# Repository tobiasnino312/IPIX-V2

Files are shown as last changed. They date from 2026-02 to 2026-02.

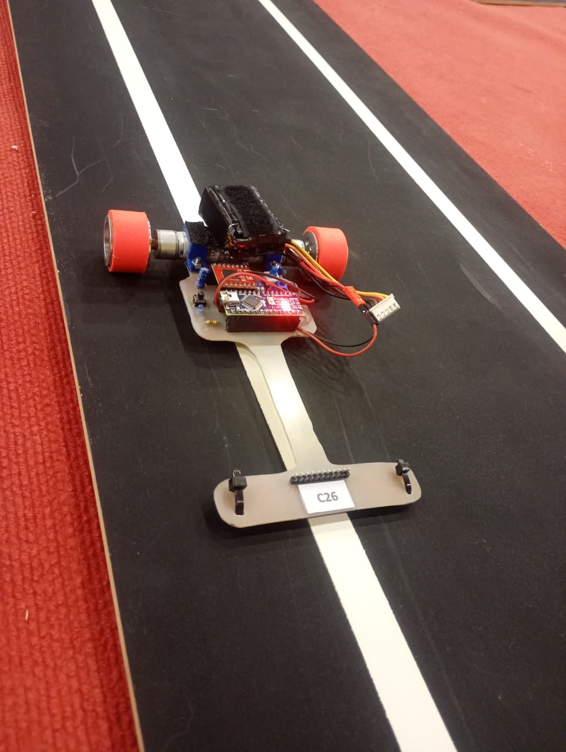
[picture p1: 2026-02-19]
IPIX_V2.jpeg

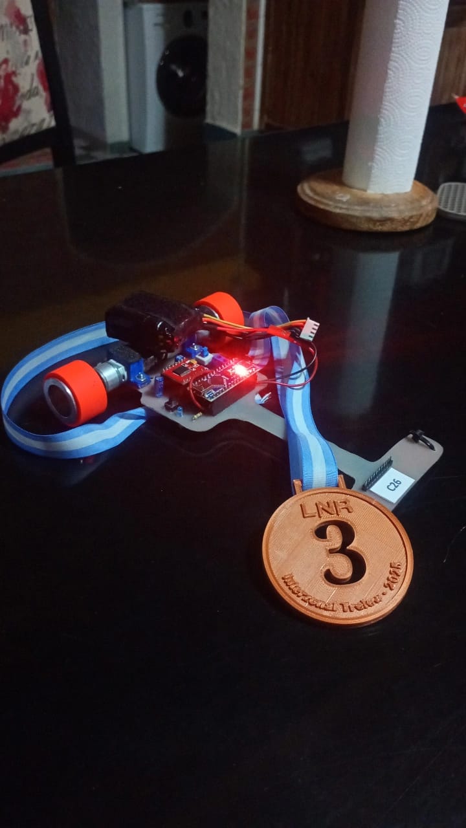
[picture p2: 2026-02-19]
IPIX_3ERO.jpeg

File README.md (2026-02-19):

# IPIX-V2
Robot seguidor de línea utilizado desde el 30/08/2025 en el interzonal de Trelew de la LNR argentina con un 3° puesto interzonal. 
El mismo trabaja con el microcontrolador Arduino Nano, TB6612FNG, motores ProFast de 4000rpm, una bateria LiPo 4s 600mAh armada casera, llantas y cubiertas JSUMO SLT20 y una regleta de sensores QTR8A genérica, similar a la de Pololu. 
Posee un switch DIP para selección de estrategias o configuraciones (empleado para cambio de velocidad según interior o exterior de la pista) y una programación basada en PID básico. 
En cuanto al código, se probó un sistema con intervalos de tiempo para el control dinámico de velocidades base/máximas o parámetros de cálculo del PID, pero debido al poco tiempo de pruebas en pista no se pudo aprovechar. Además, se está desarrollando un algoritmo con Twiddle (un algoritmo de tuning de PID con una especie de aprendizaje escalonado muy básico) que aún no fue probado en pista, con el objetivo de optimizar el tiempo de pruebas en competencia y recopilar datos de tiempo de vuelta y constantes del cálculo del PID.
Por otro lado, se está avanzando con el diseño de una tercera versión (IPIX V3) migrando a una BluePill (STM32F103C8T6), RZ7899 como drivers de motores, hueco para una turbina para mayor adherencia (la limitante actual del prototipo) y 10 sensores QRE1113 directamente soldados a placa con lectura directa por cada canal del ADC disponible.

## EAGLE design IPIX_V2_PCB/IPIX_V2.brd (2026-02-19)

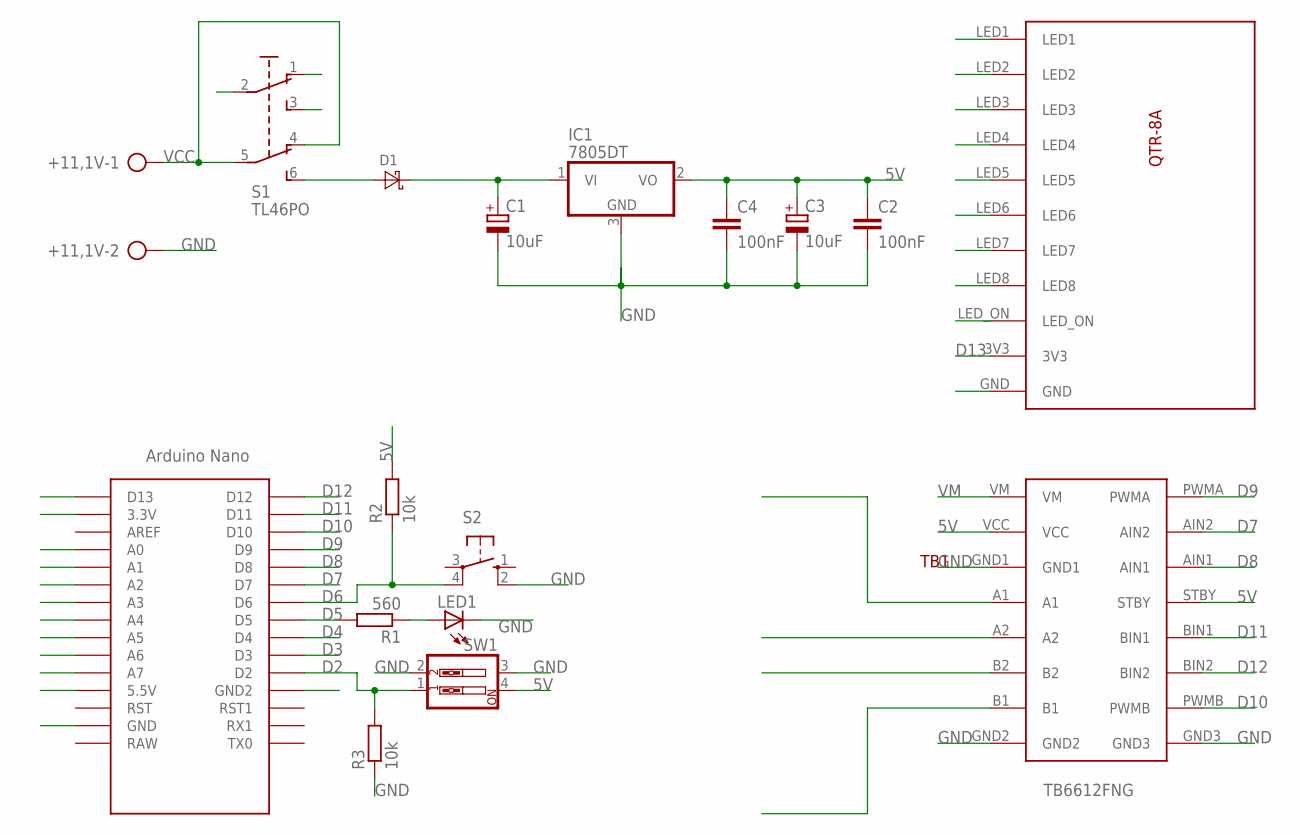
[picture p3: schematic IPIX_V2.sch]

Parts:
+11,1V: AK500/2-H
C1, C3: 10uF; E2,5-6E
C2, C4: 100nF; C0805
D1: DIODE-SCHOTTKY-DO201AD; DO201AD
IC1: 7805DT; TO252
LED1: LED3MM
R1: 560; 0204/7
R2, R3: 10k; R0805
S1: TL46PO; TL4XPO
S2: 10-XX; B3F-10XX
SW1: SW_DIP-2; EDG-02
TB1: TB6612FNG
U$1: NANO
U$2: QTR-8A

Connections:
3,3V: U$1.3.3V
5V: C2.1, C3.+, C4.1, IC1.2 (VO), R2.2, SW1.4, TB1.STBY, TB1.VCC, U$1.5V (5.5V), U$2.LED8
A0: U$1.A0, U$2.LED_ON
A1: U$1.A1, U$2.LED1
A2: U$1.A2, U$2.LED2
A3: U$1.A3, U$2.LED3
A4: U$1.A4, U$2.LED4
A5: U$1.A5, U$2.LED5
A6: U$1.A6, U$2.LED6
A7: U$1.A7, U$2.LED7
D2: R3.2, SW1.1, U$1.D2
D3: U$1.D3
D4: U$1.D4
D5: R1.2, U$1.D5
D6: R2.1, S2.4 (P1), U$1.D6
D7: TB1.AIN2, U$1.D7
D8: TB1.AIN1, U$1.D8
D9: TB1.PWMA, U$1.D9
D10: TB1.PWMB, U$1.D10
D11: TB1.BIN1, U$1.D11
D12: TB1.BIN2, U$1.D12
D13: U$1.D13, U$2.3V3
GND: +11,1V.2, C1.-, C2.2, C3.-, C4.2, IC1.3 (GND), LED1.K (C), R3.1, S1.1 (O), S1.2, S1.3 (S), S2.2 (S1), SW1.2, SW1.3, TB1.GND1, TB1.GND2, TB1.GND3, U$1.GND, U$1.GND1 (GND2), U$2.GND
unnamed: D1.A, S1.6 (S1)
unnamed 24: TB1.A2; also elsewhere on the board
unnamed 25: TB1.A1; also elsewhere on the board
unnamed: LED1.A, R1.1
unnamed 42: TB1.B2; also elsewhere on the board
unnamed 43: TB1.B1; also elsewhere on the board
VCC: +11,1V.1, S1.4 (O1), S1.5 (P1)
VM: C1.+, D1.C, IC1.1 (VI), TB1.VM

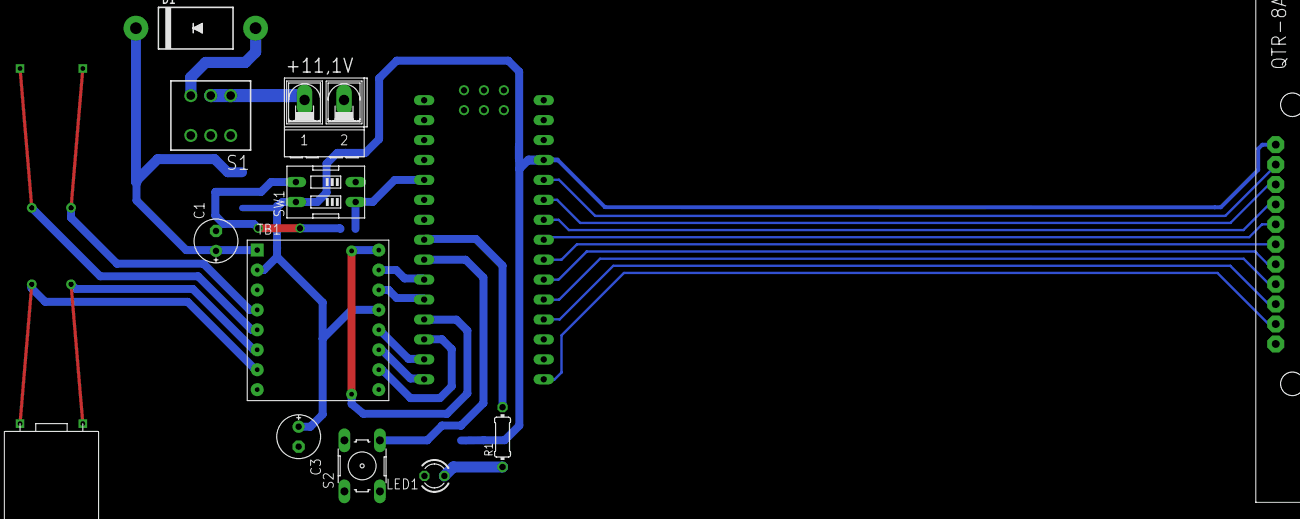
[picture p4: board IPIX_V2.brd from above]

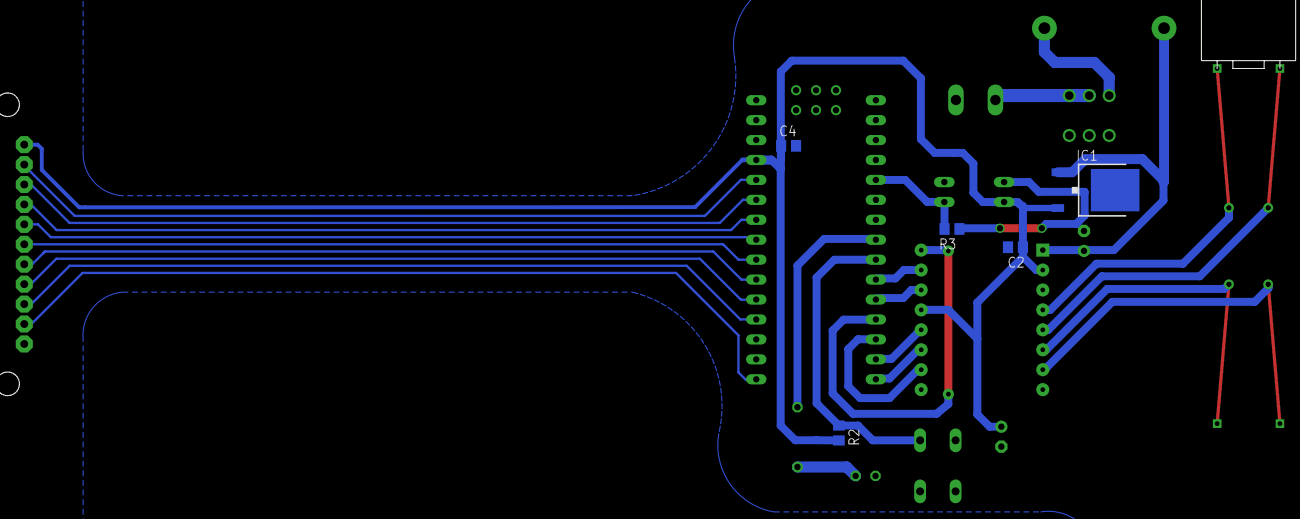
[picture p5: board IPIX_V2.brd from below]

Board: 2 copper layers, 19 parts (6 on the bottom side), 28 nets.

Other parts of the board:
U$3, U$4: MOTOR_N20

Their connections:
unnamed 24: U$3.M2; also elsewhere on the board
unnamed 25: U$3.M1; also elsewhere on the board
unnamed 42: U$4.M1; also elsewhere on the board
unnamed 43: U$4.M2; also elsewhere on the board

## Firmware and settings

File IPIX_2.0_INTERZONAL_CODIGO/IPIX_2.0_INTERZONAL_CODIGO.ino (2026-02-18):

//CODIGO UTILIZADO CON EL ROBOT IPITS 2.0 EN COMPETENCIA INTERZONAL DE ROBOTICA EL 31/08/2025 CON UN RESULTADO FINAL DE UN 3°ER PUESTO//
//LIBRERIAS//
#include <QTRSensors.h>

//SENSORES QTR8A//
QTRSensors qtr;
const uint8_t SensorCount = 8;
uint16_t sensorValues[SensorCount];

//DEFINICIONES DE PINES//
#define PWMder 10
#define IN1der 11 
#define IN2der 12
#define PWMizq 9
#define IN1izq 8
#define IN2izq 7
#define DIP 2
#define LED 5
#define BTN 6
#define IR 13

int estado=0;
int VDER, VIZQ, linea, errorant, error, integral, derivativa, velocidad, VMAX;
float kp, ki, kd, correccion;

//INTERVALOS DE TIEMPOS SENGUN SECTOR DE LA PISTA//
int tiempoinicio=0;
int tiempoactual=0;
int tiempo1=3000;
int tiempo2=999999;
int tiempo3=999999;
int tiempo4=999999;
int tiempo5=999999;
int tiempo6=999999;
int VMIN = 80;
int VEL = 80;

void setup() {
  // Fast PWM con TOP = ICR1
  TCCR1A = _BV(COM1A1) | _BV(COM1B1) | _BV(WGM11);
  TCCR1B = _BV(WGM13) | _BV(WGM12) | _BV(CS10); // prescaler = 1
  ICR1 = 999; // → 16 kHz exacto

  OCR1A = 0; // Motor A (pin 9)
  OCR1B = 0; // Motor B (pin 10)

//SENSORES//
qtr.setTypeAnalog();
qtr.setSensorPins((const uint8_t[]){A0, A1, A2, A3, A4, A5, A6, A7}, SensorCount);

//PINOUTS// 
pinMode(PWMder,OUTPUT);
pinMode(PWMizq,OUTPUT);
pinMode(IN1der,OUTPUT);
pinMode(IN2der,OUTPUT);
pinMode(IN1izq,OUTPUT);
pinMode(IN2izq,OUTPUT);
pinMode(LED,OUTPUT);
pinMode(BTN,INPUT);
pinMode(DIP,INPUT);
pinMode(IR,OUTPUT);

//ACTIVACION DE LEDS DE SENSORES//
digitalWrite(IR,1);
//LECTURA DIP//
if (digitalRead(DIP)==1){
    kp=0.35;
    ki=0.05;
    kd=38;    
    velocidad=80;
    VMAX=160; 
  }
  else{      
//I (Interior)
    kp=0.35;
    ki=0.05;
    kd=38;    
    velocidad=70;
    VMAX=140; 
  }
//ARRANQUE CALIBRACION//
while (true){
  if ((digitalRead(BTN)==0) && estado==0){
    delay(100);
    calibracion(); 
    estado=1;
    }
  if ((digitalRead(BTN)==0) && estado==1){
    digitalWrite(LED,1);
    tiempoinicio=millis();
    break;
    }
  }
}

void loop() {
  sensores();
  PID();
  MOTORES();
}

void tiempo(){
  tiempoactual = millis() - tiempoinicio;
  if(tiempoactual>=tiempo1){
    if(tiempoactual>=tiempo2){
      if(tiempoactual>=tiempo3){
        if(tiempoactual>=tiempo4){
          if(tiempoactual>=tiempo5){
           if(tiempoactual>=tiempo6){
            VMAX=170;
            velocidad=VMIN;
            }  
           else{VMAX=90;
            velocidad=VMIN;}
          }
         else{VMAX=90;
          velocidad=VMIN;}
        }
        else{VMAX=90;
         velocidad=VMIN;}
      }
      else{VMAX=90;
       velocidad=VMIN;}
    }
    else{VMAX=170;
     velocidad=VMIN;}
  }
}

void PID(){
  integral = integral + error;
  if (integral > 1000) integral = 1000;
  if (integral < -1000) integral = -1000;
  derivativa = error - errorant;
  correccion = kp * error + ki * integral + kd * derivativa;
  errorant = error;  
}
void sensores(){
  linea = qtr.readLineWhite(sensorValues);
  error = linea - 3500;
}

void calibracion(){
  unsigned long startTime = millis();
  while (millis() - startTime < 5000) { // 5 segundos de calibración
    qtr.calibrate();
    digitalWrite(LED,1);
    delay(50);
    digitalWrite(LED,0);
    delay(50);
  }
}

void motorizq(){
  VIZQ=velocidad-correccion;
  if(VIZQ>VMAX){VIZQ=VMAX;}
  if(VIZQ<0){VIZQ=0;}
  digitalWrite(IN1izq,0);
  digitalWrite(IN2izq,1);
  OCR1A = VIZQ; //PWM IZQ//
}
void motorder(){
  VDER=velocidad+correccion;
  if(VDER>VMAX){VDER=VMAX;}
  if(VDER<0){VDER=0;}
  digitalWrite(IN1der,1);
  digitalWrite(IN2der,0);
  OCR1B = VDER; //PWM DER//
}
void MOTORES(){
  motorder();
  motorizq();
}
